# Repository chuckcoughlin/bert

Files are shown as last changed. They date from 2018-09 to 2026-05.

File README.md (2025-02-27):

## bert
"Bert" is a DIY robot development project based on the open-source version of the [Poppy](https://www.poppy-project.org/en/) platform developed by [Generation Robots](https://www.generationrobots.com/en/278-poppy-humanoid-robot). Bert is a reduced stature (83cm) humanoid. The name is assigned in the hope that the robot will dance as Dick van Dyke's character in "Mary Poppins". We have a long ways to go.

 For further details see the [architecture](http://github.com/chuckcoughlin/bert/tree/master/docs/architecture.md), [toolchain](https://github.com/chuckcoughlin/bert/tree/master/docs/toolchain.md), [test plan](https://github.com/chuckcoughlin/bert/tree/master/docs/testplan.md) and [user-guide](http://github.com/chuckcoughlin/bert/tree/master/docs/user-guide.md) documents.
 The test plan contains current testing status and is a good indication of the project's progress. A prior version of the robot written in `Java` for the `Odroid-XU4` processor is stored on the `version1` branch. The current version is written in `Kotlin` for the `Odroid-N2+`

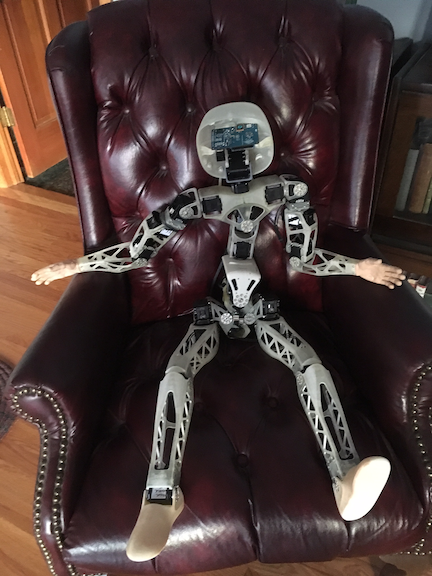
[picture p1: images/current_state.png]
Bert
 
 ```                  Bert - Most Recent Picture     ```

Video clips showing representative capabilities are available at the following links:
 * [Sample voice interaction](https://www.youtube.com/watch?v=ZoP7b5YDawg)
 * [Creating a pose](https://www.youtube.com/watch?v=3lilrxy11Ac)

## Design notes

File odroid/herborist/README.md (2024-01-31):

# Herborist
Herborist is a graphical tool that helps you detect and configure Dynamixel motors for Poppy creatures or other robotic projects. 

More precisely, Herborist can be used to:

* Find and identify available serial ports
* Scan multiple baud rates to find all connected motors
* Modify the EEPROM configuration (of single or multiple motors)
* Make motors move (e.g. to test the angle limits).

**Compatible motors:** Identical to `pypot`: MX-106, MX-64, MX-28, MX-12, AX-12, AX-18, RX-24, RX-28, RX-64, XL-320, SR-RH4D, EX-106. Derivated versions are also supported (e.g. MX-28AT, MX-28R, MX-28T, ...).

Install herborist with `pip install herborist` and run it with command `herborist`:

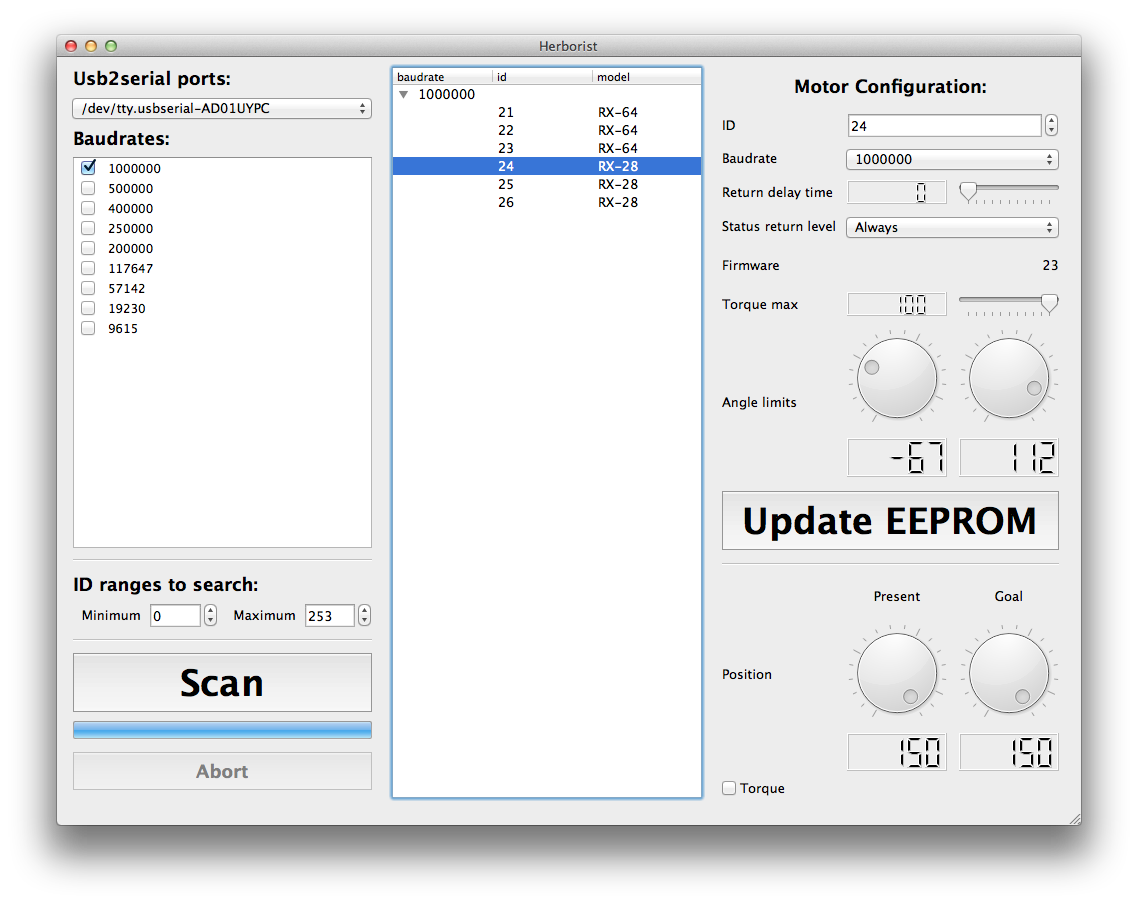
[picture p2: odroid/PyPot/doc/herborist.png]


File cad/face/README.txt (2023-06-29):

Steps to create the face model.

1) Starting with the Poppy skeleton/head/head_face.stl
2) Import 1) into Blender. Scale to mm. Set origin, rotation. Remove all non-manifold
   vertices. Save as face_raw.blend. Export as face_raw.stl.
3) Run OpenScad, blocked_face.scad. This reads head_face.stl and blocks off portions of
   the face to be saved. Export the block shapes only as blocks.stl.
4) Import 2) and 3) into Blender. Use boolean operators to save the intersection of 
   the blocks and the raw face. Clean up any block remnants. Save as collar.blend 
   and export as collar.stl.
5) Fill the top open space by selecting points around the perimeter and "new face 
   from vertices". For each of the three faces, loop-cut and separate. Save as 
   collar-face.blend.
6) From 5) Delete the collar (We will merge at the end). Merge the 3 faces into
   a single object. Lock down perimeter. Save as face-only.blend. 
7) Select the outer edge of the three planes. From the "Mesh" menu add a convex hull. 
   Delete the part of the hull that is on the backside. From the "vertex" menu
   select "bevel", in turn, for each of the two nodes that radiate a large number
   of edges. Save as "face-mesh'.

Alternate
Files named cartoon_head have been purchased from TurboSquid under their 3D Model License (https://blog.turbosquid.com/turbosquid-3d-model-license). Product ID: 1912829. "You can use the model for both non-commercial and commercial purposes. You can use it for multiple projects, forever(more informations under license)."

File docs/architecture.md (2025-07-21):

# High-level Design and Software Architecture

Control software embedded in the "Bert" project takes its inspiration from the [Poppy Humanoid](https://www.poppy-project.org) project at
[Generation Robots](https://www.generationrobots.com/en/278-poppy-humanoid-robot). Our implementation deviates significantly, however. The core language is Kotlin instead of C++ and Python. The feature-set has been greatly simplified - and we have added natural-language speech processing with the integration of an Android tablet.

The *Poppy*  project is described in detail in the thesis ["Poppy: open-source, 3D printed and fully-modular
robotic platform for science, art and education"](https://hal.inria.fr/tel-01104641v1/document) by Matthieu Lapeyre. A full list of project authors may be found at: <https://github.com/poppy-project/poppy-humanoid/doc/authors.md>.

The bulk of this document addresses various design issues and approaches to their solutions (or lack thereof)

***
## Table of Contents <a id="table-of-contents"/>
  * [Target Hardware](#hardware)
    * [Odroid](#odroid)
    * [Android](#android)
    * [Raspberry Pi](#raspberry)
  * [Software Architecture](#architecture)
    * [ANTLR](#antlr)
    * [Configuration](#configuration)
    * [URFD](#geometry)
    * [Dynamixel Servos](#dynamixel)
    * [Open AI](#ai)
  * [Design Considerations](#design)
    * [Control](#control)
    * [Messaging](#messages)
    * [Forward Kinematics](#forward)
    * [Inverse Kinematics](#inverse)
    * [Poses](#poses)
  * [Appendices](#appendices)
    * [Rationale for Kotlin](#whykotlin)
    * [Failures](#failures)

***
## Target Hardware 
[toc](#table-of-contents)

#### Odroid  
The robot's central processor is a single-board Linux computer, an Odroid N2+.

#### Android 

A Samsung Galaxy Tablet S8+, model SM-X800 is used as the speech processor. It converts spoken input into command strings used to control the robot. It also converts textual responses from tne robot into audible speech. The tablet is Android version 13, SDK version 33.

#### Raspberry Pi 

A Raspberry Pi version 5 serves as a "fine motor controller". For smaller parts, currently eyes and
eyelids.

## Software Architecture 
[toc](#table-of-contents)

Here is a diagram that shows the major software components.

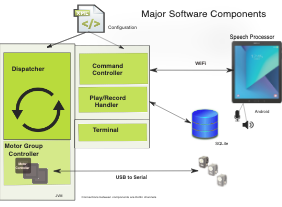
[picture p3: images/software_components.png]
Major Software Components

```                        Development - System Architecture ```

#### ANTLR  
*ANTLR* is a parsing framework explained [here](https://www.antlr.org). It is used to convert
streams of tokens from spoken text into commands for the robot.

#### Configuration 
Robot attributes and connectivity are defined in an .xml file, *bert.xml*. A representative
example is shown below.
The file is read by each of the independent processes, giving them a common understanding
of site-specific parameters and attributes of the robot.

Substitution parameters, @...@, are replaced with site-specific values during the build.
```
<?xml version="1.0" encoding="UTF-8"?>

<!-- This file describes "bert", a poppy-like robot. The identical configuration
     is used for both the server and client-side processes.
 -->
 <?xml version="1.0" encoding="UTF-8"?>

 <!-- This file describes "bert", a robot derived from the Poppy project.
 	 This identical configuration is used for each of the independent processes.
  -->
 <robot>
 	<!-- This first section lists miscellaneous properties. @...@ values are
 	     replaced by the build scripts.
 	-->
 	<property name="name">bert</property>
 	<property name="release">@RELEASE@</property>
 	<property name="date">@DATE@</property>
 	<!--  Socket port used by the bluetooth RFCOMM server  -->
 	<property name="blueserver">11046</property>
 	<!--  Cadence in msecs refers to the record frequency  -->
 	<property name="cadence">1000</property>
 	<!--  Name of machine hosting the server process  -->
 	<property name="hostname">localhost</property>
 	<!--  Used by the terminal  -->
 	<property name="prompt">bert: </property>

  <!-- For the "Command" controller, defines the bert  TCP socket. The device UUID
	     must match the hardcoded value in tablet code, the well-known bluetooth UUID
	     for RFCOMM. -->
	<controller name="command" type="COMMAND"
		socket="bert" hostname="localhost"  port="11046" uuid="1101-0000-2000-8080-00815FAB34FF">
	</controller>
	<controller name="terminal" type="TERMINAL" prompt="bert:"/>

 	<!-- These controllers manage groups of joints. Requests are sent the entire group at once across
 	     a serial connection. The names must exist in the enumeration bert.share.motor.Joint.
 	     There is an upper body group and a lower body group.
     -->
 	<controller name="lower" type="SERIAL">
 		<port  name="lower" device="@PORT_LOWER@" />
 		<joint name="LEFT_ANKLE_Y" type="MX28" id="15" offset="-91" min="60" max="135" orientation="direct" />
 		<joint name="LEFT_HIP_X"   type="MX28" id="11" offset="-8" min="155" max="205" orientation="indirect" />
 		<joint name="LEFT_HIP_Y"   type="MX64" id="13" offset="-18" min="75" max="225" orientation="direct" />
 		<joint name="LEFT_HIP_Z"   type="MX28" id="12" offset="-200" min="-20" max="45" orientation="indirect" />
 		<joint name="LEFT_KNEE_Y"      type="MX28" id="14" offset="-4" min="50" max="180" orientation="indirect" />
 		<joint name="RIGHT_ANKLE_Y"    type="MX28" id="25" offset="-108" min="60" max="135" orientation="indirect" />
 		<joint name="RIGHT_HIP_X"      type="MX28" id="21" offset="16" min="155" max="205" orientation="direct" />
 		<joint name="RIGHT_HIP_Y"      type="MX64" id="23" offset="-18" min="75" max="225" orientation="indirect" />
 		<joint name="RIGHT_HIP_Z"      type="MX28" id="22" offset="-160" min="-20" max="45" orientation="direct" />
 		<joint name="RIGHT_KNEE_Y"     type="MX28" id="24" offset="15" min="50" max="180" orientation="direct" />
 	</controller>
 	<controller name="upper" type="SERIAL">
 		<port  name="upper" device="@PORT_UPPER@" />
 		<joint name="LEFT_ARM_Z"   type="MX28" id="43" offset="0" min="-105" max="45" orientation="indirect" />
 		<joint name="LEFT_ELBOW_Y" type="MX28" id="44" offset="17" min="45" max="180" orientation="direct" />
 		<joint name="LEFT_SHOULDER_X"  type="MX28" id="42" offset="-70" min="90" max="180" orientation="direct" />
 		<joint name="LEFT_SHOULDER_Y"  type="MX28" id="41" offset="-65" min="-120" max="155" orientation="direct" />
 		<joint name="RIGHT_ARM_Z"      type="MX28" id="53" offset="0" min="-105" max="45" orientation="direct" />
 		<joint name="RIGHT_ELBOW_Y"    type="MX28" id="54" offset="4" min="45" max="180" orientation="indirect" />
 		<joint name="RIGHT_SHOULDER_X" type="MX28" id="52" offset="-105" min="90" max="180" orientation="indirect" />
 		<joint name="RIGHT_SHOULDER_Y" type="MX28" id="51" offset="-100" min="-155" max="120" orientation="indirect" />
 		<joint name="HEAD_Y"       type="AX12" id="37" offset="-120" min="-5" max="20" orientation="direct" />
 		<joint name="HEAD_Z"       type="AX12" id="36" offset="-150" min="-30" max="30" orientation="indirect" />
 		<joint name="ABS_X"        type="MX64" id="32" offset="0" min="150" max="210" orientation="direct" />
 		<joint name="ABS_Y"        type="MX64" id="31" offset="16" min="150" max="210" orientation="direct" />
 		<joint name="ABS_Z"        type="MX28" id="33" offset="-160" min="-60" max="60" orientation="direct" />
 		<joint name="BUST_X"       type="MX28" id="35" offset="5" min="150" max="210" orientation="direct" />
 		<joint name="BUST_Y"       type="MX28" id="34" offset="24" min="150" max="210" orientation="direct" />
 	</controller>
 </robot>
```

#### URDF 
The geometry of the robot is used for trajectory planning, balance and other purposes. It is inspired by the
Unified Robot Description Format](http://wiki.ros.org/urdf/XML) (URDF) file.  A sample, specific to _Poppy_, may be found [here](https://github.com/poppy-project/poppy-humanoid/blob/master/hardware/URDF/robots/Poppy_Humanoid.URDF). We have modified the format freely for our own purposes.

We have added the IMU location and taken other liberties with the standard (e.g. angles in degrees to match
the Dynamixel output). Joint orientations are defined via a unit vector showing the alignment. The axes
form a right-handed rool, pitch, yaw coordinate system as follows:

| Axis | <center>Description</center> |<center>Positive</center>
| :--: | :---------------------- | :-------------: |
| x | Front-to-back | Front |
| y | Side-to-side | Robot's Right |
| z | Vertical | Up |

Note that in order to be symmetric with respect to the vertical centerline, some
joints are defined in an inverse direction. Links are
names of the "bones" between joints. As series of joints
and links form a "limb".
```
<?xml version="1.0" encoding="utf-8"?>
<!--
	Right-handed coordinate system: x positive to front, y positive to right, z positive up
	- axis is unit vector around which joint rotates clockwise
   	- lengths ~ mm, angles ~ degrees -->
<robot name="bert">
	<!-- The Internal Measurement Unit (IMU) is the world-frame origin. Its position is always (0,0,0).
	     This origin is located in the pelvis midway between the hip sockets and back to align with the
	     left/right hip y axis. The orientation of the IMU is with respect to the robot reference frame.
	     It may be altered by setting IMU quaternion roll,pitch,yaw directly and then updating.
	-->
	<imu rpy="0. 0. 0."/>
	<!-- A link is roughly equivalent to a bone. A link connects a source pin (joint)
	     to a joint or end effector. The parent link is a joint (a REVOLUTE link pin).

	    Links form a tree from the IMU terminating in the various end effectors.
		Joint names must match the names in bert.xml.

		Link (end-pin) coordinates are relative to the source pin ~ mm. The y-axis coincides with the joint axis
		with the origin at the mid-point, positive to the left. The link z axis is always perpendicular to the joint
		axis corresponding to the y-axis "home" position, positive up. "home" is where the robot stands straight up.
		The x-axis juts forward perpendicular to the z-axis (positive forward).

		The "rpy" settings (roll, pitch, yaw) define the orientation of the motor or end-effector with respect to
		the source pin. The order of rotations is: roll, pitch, yaw. The "rpy" settings do not affect the location
		of the end-pin, only its orientation. Use right-hand rule to determine direction.
		     roll  - rotation about the x axis
		     pitch - rotation about the y-axis
		     yaw   - rotation about the z-axis

		Joints are named for the robot axis about which they rotate when viewed in the "home" position.

	  -->
	<link side="FRONT">        <!-- root -->
		<joint name="RIGHT_HIP_X"
			   xyz="0.0 22.5417390633467 0.0"  rpy="0. 0. 90." home="180.0"/>
		<joint name="LEFT_HIP_X"
			   xyz="0.0 -22.5417390633466 0.0" rpy="0. 0. 90." home="180.0"/>
		<joint name="ABS_Y"
			   xyz="12.0 0.0 62.0"             rpy="0. 0. 0." home="180.0"/>
		<source joint="IMU" />
	</link>
	<link side="RIGHT">
		<joint name="RIGHT_HIP_Z"          home="0.0"
			   xyz="43.9986 5.0 0.0" rpy="0. 0. 90."/>
		<source joint="RIGHT_HIP_X" />
	</link>
	<link side="RIGHT">
		<joint name="RIGHT_HIP_Y"
			   xyz="0.0 0.0 24.0" rpy="0. 0. 0." home="180.0"/>
		<source joint="RIGHT_HIP_Z" />
	</link>
	<link side="RIGHT">
		<joint name="RIGHT_KNEE_Y"
			   xyz="0.0 0.0 182.0"  rpy="0. 0. 0." home="180.0"/>
		<source joint="RIGHT_HIP_Y" />
	</link>
	<link side="RIGHT">
		<joint name="RIGHT_ANKLE_Y"
			   xyz="0.0 0.0 -180.0"  rpy="0. 180. 0." home="90.0"/>
		<source joint="RIGHT_KNEE_Y"/>
	</link>
	<link side="RIGHT">
		<appendage name="RIGHT_TOE"
				   xyz="95. -15.0 -35.5" rpy="180. 90. 180."/>
		<appendage name="RIGHT_HEEL"
				   xyz="-43.0 12.0 -35.5" rpy="180. 90. 180."/>
		<source joint="RIGHT_ANKLE_Y"/>
	</link>
	<link side="LEFT">
		<joint name="LEFT_HIP_Z"
			   xyz="-43.9986 5.00 0.0" rpy="0. 0. 90." home="180.0"/>
		<source joint="LEFT_HIP_X"/>
	</link>
	<link side="LEFT">
		<joint name="LEFT_HIP_Y"
			   xyz="0.0 0.0 24.0"       rpy="0. 0. 0." home="180.0"/>
		<source joint="LEFT_HIP_Z"/>
	</link>
	<link side="LEFT">
		<joint name="LEFT_KNEE_Y"
			   xyz="0.0 0.0 182.0" rpy="0. 0. 0." home="180.0"/>
		<source joint="LEFT_HIP_Y"  />
	</link>
	<link side="LEFT">
		<joint name="LEFT_ANKLE_Y"
			   xyz="0.0 0.0 -180.0" rpy="0. 180. 0." home="90.0"/>
		<source joint="LEFT_KNEE_Y" />
	</link>
	<link side="LEFT">
		<appendage name="LEFT_TOE"
				   xyz="95. 15.0 -35.5"  rpy="180. 90. 180."/>
		<appendage name="LEFT_HEEL"
				   xyz="-43. -12.0 -35.5" rpy="180. 90. 180."/>
		<source joint="LEFT_ANKLE_Y" />
	</link>
	<link side="FRONT">
		<joint name="ABS_X"
			   xyz="0.0 0.0 8.0" rpy="0.0 180.0 90.0" home="180.0"/>
		<source joint="ABS_Y"/>
	</link>
	<link side="FRONT">
		<joint name="ABS_Z"
			   xyz="0.0 12.0 51.6374742" rpy="90. 90.0 0.0" home="0.0"/>
		<source joint="ABS_X" />
	</link>
	<link side="FRONT">
		<joint name="CHEST_Y"
			   xyz="-2.8 79.85 0.0"  rpy="-90. 90. 90." home="180.0"/>
		<source joint="ABS_Z" />
	</link>
	<link side="FRONT">
		<joint name="CHEST_X"
			   xyz="0.0 8.0 0.0" rpy="90. 180. -90." home="180.0"/>
		<source joint="CHEST_Y"/>
	</link>
	<link side="FRONT">
		<joint name="NECK_Z"
			   xyz="-5.0 0.0 84.0"    rpy="90. -90. 0." home="180.0"/>
		<joint name="LEFT_SHOULDER_Y"
			   xyz="-4.0 -77.1 50.0"  rpy="0. 0. 90." home="0.0"/>
		<joint name="RIGHT_SHOULDER_Y"
			   xyz="-4.0 77.1 50.0"  rpy="0. 0. 90." home="0.0"/>
		<source joint="CHEST_X" />
	</link>
	<link side="FRONT">
		<joint name="NECK_Y"        home="0.0"
			   xyz="-0.0 20.0 20.0"  rpy="-90. 0. -90."/>
		<source joint="NECK_Z"/>
	</link>
	<link side="FRONT">
		<appendage name="LEFT_EYE"
				   xyz="0.0 32.0 55.0" rpy="0. 0. 0."/>
		<appendage name="RIGHT_EYE"
				   xyz="0.0 -32.0 55.0"  rpy="0. 0. 0."/>
		<appendage name="LEFT_EAR"
				   xyz="-30.0 62.0 55.0" rpy="0. 0. 0."/>
		<appendage name="RIGHT_EAR"
				   xyz="-30.0 -62.0 55.0"/>
		<appendage name="NOSE"
				   xyz="15.0 0.0 40.0" rpy="0. 0. 0."/>
		<source joint="NECK_Y"  />
	</link>
	<link side="LEFT">
		<joint name="LEFT_SHOULDER_X"
			   xyz="-28.4 0.0 0.0" rpy="0. 90. 90." home="180.0"/>
		<source joint="LEFT_SHOULDER_Y" />
	</link>
	<link side="LEFT">
		<joint name="LEFT_SHOULDER_Z"
			   xyz="0.0 18.5 -83.0"  rpy="0. 90. 90." home="180.0"/>
		<source joint="LEFT_SHOULDER_X" />
	</link>
	<link side="LEFT">
		<joint name="LEFT_ELBOW_Y"
			   xyz="81.175 0.0 10.0"  rpy="0. 90. 180." home="180.0"/>
		<source joint="LEFT_SHOULDER_Z" />
	</link>
	<link side="LEFT">
		<appendage name="LEFT_FINGER"
				   xyz="4.99 -6.915 -121.0" rpy="0. 90. 0.0"/>
		<source joint="LEFT_ELBOW_Y" />
	</link>
	<link side="RIGHT">
		<joint name="RIGHT_SHOULDER_X"
			   xyz="28.4 0.0 0.0" rpy="0. 90. 90." home="0.0"/>
		<source joint="RIGHT_SHOULDER_Y"/>
	</link>
	<link side="RIGHT" >
		<joint name="RIGHT_SHOULDER_Z"
			   xyz="0.0 18.5 83.0" rpy="0. 90. 90." home="180.0"/>
		<source joint="RIGHT_SHOULDER_X"/>
	</link>
	<link side="RIGHT">
		<joint name="RIGHT_ELBOW_Y"
			   xyz="81.175 0.0 10.0" rpy="0. 90. 180." home="180.0"/>
		<source joint="RIGHT_SHOULDER_Z"/>
	</link>
	<link side="RIGHT" >
		<appendage name="RIGHT_FINGER"
				   xyz="4.99 6.915 -121.0" rpy="-90. 90. -90.0"/>
		<source joint="RIGHT_ELBOW_Y" />
	</link>
</robot>
```
Some dimensions were taken from the [Poppy URDF](https://github.com/poppy-project/poppy-humanoid/blob/master/hardware/URDF/robots/Poppy_Humanoid.URDF), others were measured directly.

Analysis of this file, results in a description of the robot as a tree or
"chain" of links. The tree has a single origin in the center of the pelvis. There are
multiple terminations or "end effector" (e.g. finger or toe). The links represent limbs of the body (e.g "thigh").
A quaternion transform matrix is calculated for each link, describing its orientation and size with respect to
the parent joint.

Calculation of end-effector location is accomplished via Quaternion multiplication up the chain.

#### Dynamixel Servos  
The control motors are Dynamixel MX-64, MX-28 and AT-12A models from [Robotis](http://en.robotis.com).
The servos feature their own PID control. A single write of a target position, speed and torque is all that is
required for control. There is no need for a constant refresh action.
A further efficiency is provided by the *SYNC WRITE* directive. This allows control of multiple motors
with a single command, as long as the affected motors are daisy-chained on the same serial port. A
*SYNC WRITE* command does not return status.

We use version 1.0 of the protocol as the motors were delivered with that version.

Idiosyncrasies:<br/>
  * There appears to be a maximum write frequency, especially for the AT-12A motors. We guarantee at least 50ms between consecutive writes to the same serial port. The symptom is dropped responses.
  * There is no guarantee that responses from the serial port correlate 1:1 with the requests. The
   response buffer can hold partial replies or several replies combined.

#### Open AI  
 The interface with [Chat GPT](https://openai.com/chatgpt/overview)  is incidental to the operation
 of the robot. It is used simply to add completion to queries or commands that would be otherwise not understood
 by the robot. In order to use the AI interface you must create an account and obtain a key from from `Open AI`
 and place it in the environment on the robot (e.g. in ~/.bashrc) as CHATGPT_KEY.

## Design Considerations <a id="design"/>

#### Control <a id="control"/>
[toc](#table-of-contents)

The main robot process is a Kotlin application running on the Odroid processor.
Major components, _terminal_,_command_, and _dispatcher_ are Kotlin co-routines
communicating over Channels. The messages passed back and forth between these processes are instances of class _MessageBottle_.
Communication with the tablet process is via text messages across a Wi-Fi
socket.

There are numerous situations in the robot where a single user command results in multiple motor commands internally. For example, whan the robot has been relaxed,
all positional information is lost. So when re-enabling torque, the joint angle information must be re-read to keep it up-to-date.
Another example is *pose* commands that are split into separate
directives for each limb.

Moreover, it is important tnat the ``MotorController`` not be given a command until the serial callback of the previous has been received.
A new request must not
submitted until the ``MotorConrtoller`` finishes with the previous request.
The sequencing function as well as command expansion is handled by an ``InternalController`` which queues requests and inserts required supporting requests as necessary.

#### Messaging
The tablet executes a Wi-fi client based on Java classes that are a standard part of the Android SDK. It connects to the robot process via sockets.

Messages that are intended to be spoken or logged are prepended
with a 4-character header followed by ASCII text.
Messages have a 1K-byte
size limit and are stripped of any trailing whitespace except for a terminating new-line.

More complicated messages intended for inter-process communication have
a similar header followed by a string indicating type and then JSON
text.

Header values are described in the table below:

| Header	| <center>Description</center>|
| -------- | :------------------------------------------------------------------ |
|MSG:|	Message from the tablet to the robot. Plain english request or query.	|
|ANS:|	Reply from the robot. This text is meant to be spoken and appear on the transcription log. |
|JSN:|	Communicate via JSON objects. These messages direct robot-tablet communication, not meant for enunciation.	|
|LOG:|	System message from the robot meant to appear on the tablet's log panel. |
|TBL:|	Define a table to show on the tablet's table panel. Pipe-delimited fields contain: title, column headings. |

Several messages may be buffered in the same socket transmission to or from the tablet. However, the
sender appends a new-line to each message to enable both the tablet and robot
Kotlin code to use a custom `readline()` routine to parse one message at a time.

#### Forward Kinematics 
Forward kinematics refers to the calculation of the 3D position of joints and end effectors based
on the connections of skeletal components and joint angles. The calculations are derived from
<ins>Introduction to Robotics</ins>  by S. K. Saha and
facilitated by the blog post [How to Calculate a Robot's Forward Kinematics in 5 Easy Steps](https://blog.robotiq.com/how-to-calculate-a-robots-forward-kinematics-in-5-easy-steps) by Alex Owen-Hill.

Refering to the URDF.xml file (listed above) *link* elements:

| Parameter	| <center>Description</center> |
| -------- | :------------------------------------------------------------------ |
|d| distance from the link's source pin to the REVOLUTE center in the z direction. |
|r| length of the common normal between source and link center z axes|
|alpha| the angle along the common normal between previous and current z axis |
|theta| the angle of the limb x axis with respect to the source pin|
|xyz| coordinates from source to REVOLUTE center |

Lengths are ~mm, angles in degrees. The z direction is always the axis of rotation of the motor.

#### Inverse Kinematics 
Optimal trajectory planning, such as the Poppy example [here]
(https://github.com/Phylliade/ikpy/tree/master/src/ikpy) by Pierre Manceron is known to be complex and slow. We go to great lengths to avoid it.

#### Poses 
A "pose" is a position of the robot as a whole, comprising settings for each of its joints. Poses may be
generated offline or as a result of recording joint values when the robot has been manually positioned for some
purpose.  For each joint, the pose records torque, speed and position. Torque and speed are in percent
of maximum and position is in degrees. Torque is a measure of how pliant the joint is. Speed refers to
how fast the motor will move to the desired position. All values are integers. Null values
imply that the current setting will not be changed. Not all parameters are required.

| Name	| Parameter	| ABS_X	| ABS_Y |	ABS_Z ...
| -------- | --------- | ------- | ------ | ------
|relaxing|	torque	|0	|0
|standing|	position|	0	|90
|standing|	speed	|25|	null
|standing|	torque	|100|	75

``Partial View of a Sample "Pose" Table``

In the sample database table shown above, only 3 of the 25 actual joints are shown. The "relaxed" pose contains
only the single line to set torque to a zero setting. This effectively renders the robot limp.
The "standing" setting defines all three parameters. Note that the ABS_Y speed is null. This
means that for ABS-Y the speed at which it travels to 90 degrees is the same as the last
time the joint was used. On power-up speeds are 100% and torques are 0%. Unless specified in
the pose, torques are automatically set to 100% whenever a joint is moved.

When moving to a set pose, it is usually sufficient to simply use that pose as a goal and move
to it directly using a single command to the servos. For the most part, collision conflicts are
avoided by limits on the angular motion of the joints.  For situations not covered in this way, we have adopted a simple set of heuristic tests that are applied prior to each movement. In general,
these heuristics insert intermediate poses to avoid conflicts en route or truncate motion when the goal
is itself a conflict. We avoid a full trajectory optimization.

*** Raspberry Pi ***</br>
An additional processor, a Raspberry Pi, is placed in the
cranium on top of the main Odroid processor. The RPi
is a "fine motor controller" used for control of smaller
appendages, e.g. eyes.

## Appendices 
[toc](#table-of-contents)
#### Why Kotlin?
In the "Poppy" [thesis](https://hal.inria.fr/tel-01104641v1/document) (section 7.4.1 and following), the author considers use of the Robot Operating System (ROS) for the core software and concludes that it is overly complex and inefficient. This coincides with my own experience with [sarah-bella](https://github.com/chuckcoughlin/sarah-bella). Moreover, I discovered that, at least with Android, ROS messaging was not reliable. Messages were dropped under high load, a situation not acceptable for control applications.

This same author noted that the "Pypot" software developed in Python for Poppy had severe performance limitations that placed strict limits on its design.

While I can't simply try all the designs, [YARP](http://www.yarp.it/index.html) used by the "iCub" project seemed closest to my perceived needs. It is written in C++ and is loaded with features that I'll never use. Given my failure to create a cross-compilation environment, I've decided to let a simplified *YARP* serve as an inspiration for a Kotlin-based solution. For simplicity, the ancillary code will be Kotlin also.

The previous version was written entirely in Java. However I decided to
write the current iteration of the project in Kotlin for the following reasons:
  * The Android platform identifies Kotlin as a core language
  * The threading model seems much more straightforward
  * It is possible to automatically convert Java to Kotlin
  * It was time for me to learn something new

Why did I select Java for the original project when the iCub project chose Python?
  * Familiarity - over 2 decades of working with Java
  * Refactoring - the refactoring capabilities of IntelliJ are unparalleled, in my opinion, and make code re-structuring quick, easy and accurate
  * Code-Debug-Cycle - problems are more likely to be discovered by the compiler rather than run-time as with Python
  * Debugging - via IntelliJ we can set breakpoints and inspect run-state not only locally, but on the target robot
  * Performance - Java executes an order of magnitude faster than Python
  * Threading - the Java threading model is more straightforward (IMHO)
  * Cross-compiling - difficulties creating Odroid executables precluded my use of C++.

### Failures 
[toc](#table-of-contents)

This section documents ideas that were tried and abandoned. The implication here is not
so much that these ideas won't work, but rather that I couldn't get them to work or found
more expedient alternatives.

*** Gradle *** <br/>
``Gradle`` is a modern tool for building software of several flavors.  To install ``Gradle`` use ``homebrew``:
```
     brew install gradle
     brew install gradle-completion
```
I totally failed to create a C++ build script for cross-compilation (Mac to Odroid). Moreover after nearly a week of trying, I gave up on the Java building also. I was unable to create an environment to conveniently share re-usable code among separate top level targets. I'm sure it can be done, I just lost interest. *ant* does everything I need.

*** Cross-compilation *** <br/>
On the build machine, I downloaded [GNU Embedded Toolchain for ARM]( https://developer.arm.com/open-source/gnu-toolchain/gnu-rm/downloads), then followed the installation steps outlined [here](https://gnu-mcu-eclipse.github.io/toolchain/arm/install/#macos-1), Using a *makefile* and these tools, I compiled C++ code for the Odroid X64. It had a bad format and didn't execute. I gave up on C++ in favor of Java for the core control loop.

*** Cmake *** <br/>
The [TinyB](https://github.com/intel-iot-devkit/tinyb ) library for Bluetooth integration came with build files for *cmake*.
I was unable to get a successful compilation of the JNI code on the Odroid. I followed the directions [here](http://fam-haugk.de/starting-with-bluetooth-le-on-the-raspberry-pi) and [here](http://www.martinnaughton.com/2017/07/install-intel-tinyb-java-bluetooth.html) with
modifications for the Odroid and Java11. With these installs which literally took
hours and used up over 10% of available disk space,  the _cmake_ build still never completed successfully.
```
sudo apt-get install libgtk2.0-dev
sudo apt-get install pkg-config
sudo apt-get --purge autoremove cmake
sudo apt-get install build-essential
cd ~
wget http://www.cmake.org/files/v3.14/cmake-3.14.0.tar.gz
tar -xzf cmake-3.14.0.tar.gz
cd cmake-3.14.0
./configure
make
sudo make install
hash -r

export JAVA_AWT_LIBRARY=$JAVA_HOME/lib/libawt.so
export JAVA_JVM_LIBRARY=$JAVA_HOME/lib/server/libjvm.so
export JAVA_INCLUDE_PATH=$JAVA_HOME/include
export JAVA_INCLUDE_PATH2=$JAVA_HOME/include/linux
export JAVA_AWT_INCLUDE_PATH=$JAVA_HOME/include
```
Since the purpose of all this was to generate a Makefile of about 50 lines, I
did it the old-fashioned way and edited it by hand, to use `make` directly.

*** Herborist *** </br>

Herborist is a tool for configuring Dynamixel servos. The [toolchain](https://github.com/chuckcoughlin/bert/tree/master/docs/toolchain.md) document describes an Ubuntu installation using *pip*, but, for me, the install of the PyQt5 package failed and, subsequently, the *herborist* install. As a workaround, I copied the code (pure python) and ran it directly.
```
   cd
   cd src/herborist
   python3 setup.py build
   sudo chmod 777 /usr/local/lib/python3.10/dist-packages
   sudo chmod 666 /usr/local/lib/python3.10/dist-packages/easy-install.pth
   sudo chmod 777 build.bdist.linux-aarch64
   sudo chmod 777 /usr/local/bin
   python3 setup.py install
```
This failed to run, also. My workaround is to use a command-line tool in the *PyPot* distribution for servo
configuration.

*** JBlueZ ***<br/>
JBlueZ](http://jbluez.sourceforge.net/)
by Edward Kay is a minimalist
implementation of a Bluetooth interface. Its intent is to use JNI and link directly
to _libbluetooth.so_. However, it requires J2ME which is not the Java on the Odroid.
It also relies on _DBus_ which is yet-another-interface to learn and debug. It
also comes with a GPL license.

The version1 code had this working, but broke with the current Bluetooth version (BlueZ 5.48). Instead of
debugging yet again, we elected to drop Bluetooth communication in favor simple socket-socket communication
over WiFi. The realization that a WiFi network could be established anywhere with a cell phone "local hotspot"
removed the need for bluetooth between robot and tablet.

Programmatic access to Bluetooth requires a interface to the Odroid's
bluetooth library `libbluetooth.so` .
An excellent introduction is a book by Albert Huang
of MIT published [here](http://people.csail.mit.edu/albert/bluez-intro/).
 Starting with Albert's examples and relying
heavily on lessons learned trying to implement the various packages
mentioned in my "Failures" section (See [Software Architecture](http://github.com/chuckcoughlin/bert/tree/master/docs/architecture.md)), I developed a custom, minimalist
daemon using RFCOMM. It communicates with the Kotlin application over sockets and
the tablet via Bluetooth.
Its sole purpose is to transfer strings between the tablet and the Odroid robot application.
The tablet uses standard Android Bluetooth classes.

On the development machine, in the _IntelliJ_ Configuration project, the ``install_odroid_source`` script
copies C source files onto the Odroid in preparation for building _blueserverd_, the
daemon, and _blueserver_, an interactive test application. (This script may have to be modified for
the correct robot home directory on the Odroid).

Then to build on the Odroid, from the directory containing the source projects -
```
  cd blueserver
  make -e
  make install
  cd ${BERT_HOME}/bin
  sudo ./install_blueserver_init_scripts
```

Configure Bluetooth using the robot's pull-down menu. Configure the adapter so that it is always visible (discoverable) and give it a "friendly"
name of "bert". Pairing is based on the friendly name and can be initiated
either from the robot or the tablet. The ```bluetoothctl``` tool is available for command-line configuration.

Add the following lines to _/etc/dbus-1/system.d/bluetooth.conf_ under ``<policy context="default">``:

```
  <allow send_interface="org.bluez.GattService1"/>
  <allow send_interface="org.bluez.GattCharacteristic1"/>
  <allow send_interface="org.bluez.GattDescriptor1"/>
```

Note that _blueserver.h_ has the bluetooth address of the tablet hard-coded. On the tablet
the device should be configured as ``bert``. On the Odroid the adapter is also known as ``bert``.

The init script launches the _blueserverd_ daemon. Connection difficulties may arise if too many bluetooth-enabled
devices are in range leading to incorrect pairings. If so, the Odroid system may report
"DbusFailedError: host is down".

*** TinyB *** </br>
[TinyB](https://github.com/intel-iot-devkit/tinyb ) is a library and Java classes for Bluetooth LE communication.
 The original distribution builds with `cmake`, but I was never
able to get that working. I just created a custom `Makefile` to build the code.
and integrate it with the main robot application.

Unfortunately when loading the JNI library ...
```
      UnsatisfiedLinkError:  g_cclosure_marshall_generic
        in tinyb.BluetoothManager.getNativeAPIVersion
          BluetoothManager.getBluetoothManager
```
The underlying issue is that the missing method was introduced in libc6 2.30.
The Odroid has 2.27. I get this error on all native methods. I assume it is a
result of using C++ in the interface library.

*** Bluecove ***</br>
*BlueCove* is yet another Bluetooth library available from [here](https://code.google.com/archive/p/bluecove/wikis/Documentation.wiki). A well written example for a simple connection is written by [Luu Gia Thuy](
https://github.com/luugiathuy/Remote-Bluetooth-Android/blob/master/RemoteBluetoothServer/src/com/luugiathuy/apps/remotebluetooth)

Unfortunately the project jar files contained too many dependencies to modularize into Java 10 jars.
I decided to build the jar from scratch, adding classes as necessary. I converted logging to java.util.logger (removing _log4j_ dependencies). I removed the Java dependency on J2ME.

The standard jar files included the "stacks", native library code for different target architectures,
though not the one we needed, for ARM. Consequently I had to build from source using code
that brought on a GPL dependency.

This just got too complicated.

*** GATT *** <br/>
Since we don't need a full-featured Bluetooth interface, the idea was to simplify things
considerably by making use of GATT (Generic Atributes)
Bluetooth profiles. The only characteristics we require are two to read and write
simple strings. Following instructions [here](https://stackoverflow.com/questions/25427768/bluez-how-to-set-up-a-gatt-server-from-the-command-line), we attempted to create a GATT server on the Odroid using
 _bluetoothctl_. The reported syntax for setting service characteristics in _bluetoothctl_
 didn't work and I was never successful in creating a registration.

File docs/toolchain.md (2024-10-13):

# Skeleton and Toolchain

This document describes the software tools used to develop "Bert", including their procurement and configuration. It also gives a step-by-step guide to assembly of the skeleton, including visual aids.

"Bert" is a based on the [Poppy](https://www.poppy-project.org) platform from
[Generation Robots](https://www.generationrobots.com/en/278-poppy-humanoid-robot).  *Poppy* is supplied in open-source format, both hardware and software. Version 1.0.2 source is at: <https://github.com/poppy-project/poppy-humanoid>. The repository contains both hardware and software components plus full assembly instructions.

bert
```                        Bert Supported by Scaffolding```

***
## Table of Contents 
  * [Hardware](#hardware)
    * [Skeleton](#skeleton)
    * [Joints](#joints)
    * [Tablet](#tablet)
  * [System Setup](#system)
    * [Android](#androidprep)
    * [Odroid](#odroid)
  * [Software Development](#software)
    * [IntelliJ](#intellij)
    * [Android Studio](#android)
    * [Other Tools](#other)
***
## Hardware 
Details of the hardware assembly are documented in [The Assembly Guild for the Poppy_Humanoid](https://docs.poppy-project.org/en/assembly-guides/poppy-humanoid)

### Skeleton 
[toc](#table-of-contents)

The skeletal print-files provided by GenerationRobots are in .STL format. This form is printable directly, but not conducive to modification.

![Bert Skeleton](/images/skeletal_assembly.png)
```                  Newly Assembled Skeleton     ```

Excellent assembly instructions may be found [here](https://github.com/poppy-project/poppy-humanoid/blob/master/hardware/doc/en/assemblyGuide.md). The
videos include step-by-step procedures for each motor group.
The following sections contain describe modifications we've made to the original instructions, if any.

#### Legs 
US child-size 8 shoes seem to fit. I used a 3D print coating, [XTC-3D](https://www.smooth-on.com/products/xtc-3d/) to effect a smooth, shiny finish on the feet.

#### Arms 
The hands are coated in [UreCoat](https://www.smooth-on.com/product-line/urecoat/) which gives a rather creepy-feeling soft latex covering. A flesh-toned [colorant](https://www.smooth-on.com/category/color-and-fillers/) was mixed into the coating before application.

#### Torso 
We used 2.5 x 12mm screws to fasten the 2 SMPS2Dynamixel boards to the torso. The video shows sticking them on with hot-glue.

We applied 12V power to each SMPS2Dynamixel separately from our power supply. There is no connection between SMPS2Dynamixel boards on the RS485 ports as shown in the assembly video. The RS485 port from the upper SMPs2Dynamixel board is used to power the 12V Odroid board.

We found that the hip y joints opened too far when there was no power applied. This resulted in tangled legs that interfered with each other causing excess stress on the wiring and serial connection errors.
Rubber bungee cords are used to bring the legs to a parallel position at rest.

![Leg Supports](/images/bungee.jpg)
```                  Flexible Leg Supports     ```

#### Head 
The head design was revised in our latest version to accommodate the Odroid N2+ processor.
In the photos, the revised head is gold in color.  

A frontal view of the skull:
![Skull Front](/images/revised_head_front.jpeg)
```                  Skull Front View     ```

A back view of the skull before cabling is attached :
![Skull Back](/images/revised_head_back_unplugged.jpg)
```                  Skull Back View     ```

The umbilical cable bundle extends from the rear-end of the head to torso. It includes:
 * 12V cable for power to Odroid
 * USB extension bundle for USB2Serial
 * HDMI 8" extension to save wear and tear on Odroid HDMI port

Here are two views of the bundle from the back:
 ![Umbilical undle1](/images/umbilical1.png)
 ```                  Processor Connections     ```

 ![Umbilical undle2](/images/umbilical2.jpg)
 ```                  Umbilical Bundle     ```

 And finally we show the back view with cabling attached and dongles inserted :
 ![Skull Back Wired](/images/revised_head_back.jpeg)
 ```                  Skull Back View     ```

#### Power Supply 
12V power for the Odroid processor is supplied directly through a custom cable. Note that
the outermost wire is connected to the outside sheath of the power connector.

![12V Processor Power](/images/12V_power_cord.png)
```                  12V Processor Power     ```

The main power pack, shown below, is constructed from a 3D-printed box (source code included). Inside it contains 2 AC/12V DC converters. The 12V connectors plug directly into the back of the robot.

![Power Supply](/images/power_supply.png)
```                  12V DC Power     ```

![Power Supply Mounted](/images/power_supply_mounted.png)
```                  Power Supply Mount     ```

### Joints 
[toc](#table-of-contents)

The [pypot](#pypot) python package must be installed on the Odroid to configure and test the Dynamixel motors.

The Dynamixel setup for flashing EEPROM is shown below:

![poppy](/images/dynamixel_configuration.png)
```                        Dynamixel Flashing Setup```

More detailed information may be found [here](https://docs.poppy-project.org/en/assembly-guides/poppy-torso/addressing_dynamixe)
```
python3 /usr/local/lib/python3.10/dist-packages/pypot/tools/dxlconfig.py
```
Initially, the devices can be found with the following parameters:
```
    Port:       /dev/tty/ACM0
    Protocol:   MX
    USB Device: USB2AX
    Baud rate:  57600
    ID       :  1
```

<em> Note: When the motors were fresh from the manufacturer, I used Robotis [Dynamixel Wizard](http://www.robotis.us/roboplus1) on a Windows machine to make the initial ID and baudrate settings.  Once a motor is configured, use ``dxl_write`` for further setup.</em>

In the motor EEPROM and RAM configuration, angles are defined such that 0 deg is at the bottom when viewing the front of the motor, 180 deg is to the top. Values decrease going clock-wise. Thus, for our purposes, decreasing values of position, load and speed all refer to the clock-wise direction.
Refer to the worksheet in the *git* repository at ``cad/DynamixelConfiguration.ods`` to find id and angle limit settings for each motor. In each case, set the baud rate to 1000000 and return delay time to 0.

In order to correct for a consistent user-view of position, joints may be corrected for orientation and given a fixed offset. A joint configured as *indirect* might be considered as if viewed from the back-side. The corrections give the following meanings to angular positions. These definitions should apply equally to joints on both sides of the body.

| Axis | <center>Description</center> |
| :--: | :---------------------- |
| x | Front-to-back |
| y | Side-to-side |
| z | Vertical |

| Joint | <center>Definition</center> | Min Angle | Max Angle |
| :------ | :--------------------------------------------------- | --------: | ---------: |
| Abs(x) | Angle of side-to-side bend of the torso. 180 is straight, lower values are to the right. | 150 | 210 |
| Abs(y) | Angle between the torso and pelvis, front-to-back, measured frontwards. | 150 | 210 |
| Abs(z) | Angle of twist in the torso. Zero is no twist. Positive is toward the right. | 45 | 45 |
| Ankle | Angle between the bottom of the foot and shin, frontwards.| 45 | 180 |
| Arm(z) | Degrees of twist of upper arm. Zero is straight ahead with the palm inward. Positive is outward. | -45 | 45 |
| Bust(x) | Angle of side-to-side bend of the upper body. 180 is straight, lower values are to the right. | 150 | 210 |
| Bust(y) | Angle between the chest and torso, front-to-back, measured toward the front. | 150 | 210 |
| Elbow | Angle between the upper and lower arms, measured frontwards. | 45 | 180 |
| Hip(x) | Angle of spread of thighs. 180 is straight down, decreases as the spread increases. | 155 | 205 |
| Hip(y) | Angle between the torso and thigh, in front. 180 is straight, 90 is forward, horizontal. | 75 | 225 |
| Hip(z) | Twist of leg with respect to torso. Zero is straight ahead. Negative is knock-kneed. | -45 | 20 |
| Knee | Angle between the thigh and lower leg, measured toward the back. | 50 | 180 |
| Neck(y)| Degrees the head is tipped. 0 is horizontal, positive is up. |-5|20|
| Neck(z)| Angle the head is facing. 0 is straight ahead, positive to the right. |-45|45|
| Shoulder(x) | Angle of spread of the arms. 180 is straight down, 90 is straight out to the side. | 90 | 215 |
| Shoulder(y) | Angle between the upper arm and chest. 180 is straight down, 90 is forward, horizontal. | 0 | 225 |
<center>``Angular Position Definitions``                     </center>

## System Setup <a id="system"/>
### Android 
[toc](#table-of-contents)

##### Persistent Storage
Configuration parameters, vocabulary and other data that are meant to be stored long-term reside in a SQLite database accessible through the tablet application.
Run the following scripts in order to prepare a SQLite database on the MacOSX development system to be accessible when running the Android Studio simulator with Android production code. In the
source ``install`` directory:

``./android_dev_data_dir.sh``
``./android_dev_db_setup.sh``

Note that the system must be restarted after the
first script.

##### Transfer to Tablet
In order for the application to be transferred to the tablet from the build system, the tablet must be connected via USB. Use the same USB cable that is used to charge the device.

The tablet must also be set in "developer" mode. This is accomplished under Settings->About Tablet->Software Information. Tap on "Build number" 7 times. (Yes, really). Under Settings->Developer options, enable USB debugging. Once the cable is connected a dialog should popup asking you to allow file transfer. (If this does not appear, you may have to fiddle with Developer options->USB Configuration).

On the build system, configure Android Studio (Tools->Run>Edit Configurations) to target the build output directly to a USB device. After a successful build, merely select the "run" button to transfer the **apk** executable to the tablet.

#### Tablet 

The tablet is a 12" Samsung Galaxy S8 running Android 13.0, API level 33. Android was chosen for its
speech capabilities. All speech analysis is done on the tablet hosting both text-to-speech and a speech
recognizer. At one time the tablet become stuck in headset mode. As a workaround, we bought an external
speaker that can ultimately be located in the head.

Make sure to update the language packages (Settings->General management->Language packs) and Google Speech Recognition and Synthesis application. The application is configured to speak English with a British accent. The voice is female (I'd prefer male).

### Odroid 
[toc](#table-of-contents)

##### Initial Configuration
The following sections describe setup of the main processor on the robot, an Odroid-N2+ running Linux, described [here](https://wiki.odroid.com/odroid-n2/odroid-n2). The initial board setup used an eMMC preloaded with Ubuntu Mate 22.04 purchased directly from [HardKernel](https://www.hardkernel.com/product-category/memories. Installation was very straightforward.

Unfortunately during an upgrade to Ubuntu 4.9.1, due to a supposed error in the kernel, we lost our wi-fi driver, effectively isolating the robot system and making it useless. To recover, we downloaded the image from [here](https://wiki.odroid.com/getting_started/os_installation_guide#operating_systems_we_re_providing), then flashed using `balenaEtcher` and an eMMC Reader board per instructions [here](https://linuxhint.com/etcher-image-writer-ubuntu-burn-images/). The Ubuntu desktop versions with Mate refused to copy to our eMMC (too big?). However the Ubuntu 22.04-4.9-minimal-odroid-n2 image flashed successfully. The text below describes setup from the minimal configuration.   

The N2 has 4 USB slots that are used for:
 * Keyboard/Mouse
 * WiFi
 * Bluetooth
 * USB2AX (2)

If the boot selector switch is to the left, startup will boot into Pettiboot. To boot from the SD card, move the switch to the right. The filesystems are pre-configured with the root at 64gb, 96% free. Place all user directories under `/home`.

#### Users
The initial root password is `root/odroid`. Change password to provide some minimal security. As `root` add an administrative user `odroid/odroid`.
Create a user for the robot's use . Call it `bert`. Add these to the `sudo`, `dialout` and `uucp` groups. For example:
```
   adduser bert
   usermod -aG sudo bert
   mkdir /home/bert/robot
   mkdir /home/bert/robot/src
```
Add the following to ``~/.bashrc`` and equivalent to ``~/Library/LaunchAgents/environment.plist``:
```
   PS1="\u: "
   export BERT_HOME=/home/bert
   export ROBOT_HOME=/home/bert/robot
   export JAVA_HOME=/usr/lib/jvm/java-11-openjdk-armhf
   export PATH=${PATH}:${BERT_HOME}/bin:${BERT_HOME}/.local/bin:${JAVA_HOME}/bin
```
#### Initial Network
The wi-fi connection must be configured before any additional packages can be installed. Our wireless interface is `wlan0`. The command
```
   nmcli device wifi connect "SSID" password "PASSWD"
```
should result in a wireless connection to the internet. (Substituting name and password for the local network,
of course). A reboot may be required. As soon as the network was live, I was presented with an invitation to upgrate to release 24.04.1. I proceeded with the upgrade, only to once again lose the wifi and had to start over again. The lesson here is to avoid the temptation to upgrade to 24.04.1.

Once a WiFi connection has been made, again as `root`,
```
  apt update
  apt upgrade -y
```

then install the `Budgie` desktop. The use of `aptitude` is required because of a dependency issue (which appeared common to all desktops I tried).
```
  add-apt-repository ppa:deadsnakes/ppa
  apt install aptitude
  aptitude install ubuntu-budgie-desktop
  apt install nautilus gnome-terminal
  shutdown -r now

```
If starting from a purchased SD card, remove the `Mate` desktop.
```
  apt purge mate-desktop --autoremove
```

#### Further Configuration

Now that a wi-fi connection is established and desktop installed, continue the configuration tasks that are required even with the pre-looaded SD card.

Set the hostname to `bert`.
```
  hostnamectl set-hostname bert
```

Set the timezone:
```
  timedatectl set-timezone America/Denver
```

 Configure a static IP address. This allows us to connect to the robot even if it comes up "headless". Using the Budgie desktop, under the main menu network icon, Network Settings, edit the WiFi connection via settings icon. On the IPV4 tab, change the Method: to "Manual". Add a static address, e.g. 10.0.0.42; 255.255.255.0; 10.0.0.1. Depending on the network, another common address choice might be: 192.168.1.42. In the same dialog, set Domain Name Servers, comma-separated.
```
  75.75.75.75
  75.75.76.76
```
Validate these setting by inspecting another machine on the same network.

Restart the `odroid`. When running again,
make sure you can ping the new address from a different machine.

Next, make sure these lines exist in `/etc/ssh/sshd_config`.
```
PubkeyAuthentication yes
AuthorizedKeysFile .ssh/authorized_keys
```

Then on each development system on the network, generate SSH keys (if not already done).
```
  ssh-keygen  (use default location, no password)
```
Also on each remote system, add to `/etc/hosts`:
```
  10.0.0.42 bert
```
Also on each remote system (appropriately replacing the username),
```
  cd ~/.ssh
  ssh-copy-id -i id_rsa.pub bert@bert
```
If there are old references to `bert` in *known_hosts*, they must be deleted.

Upgrade the operating system for any changes since the image was posted and install missing tools. If these *apt* commands repeatedly throw your wi-fi router off-line, you may be forced to execute them using a direct ethernet connection. These must be run as root (or sudo).

In the `Software Sources` application, enable main (canonical free and open source software)
```
  apt update
  apt upgrade -y
  apt autoremove -y
  apt autoclean -y
  apt install rsync
  apt install sqlite3
  apt install libjssc-java
  apt install libbluetooth-dev
  apt install build-essential
  apt-get install manpages-dev
```
```
   add-apt-repository ppa:xtradeb/apps -y
   apt update
   apt upgrade
   apt install chromium
   apt install firefox
```

As super-user, set the serial port permissions by creating file `/etc/udev/rules.d/50-ttyusb.rules` with the following contents:
```
KERNEL="ttyACM*",MODE="0666"
```
Reboot then as root:
```
  chmod 666 /dev/ttyACM*
``

In `/etc/ld.so.conf.d`, add a file named `bert.conf` containing the single line:
```
  /home/bert/robot/lib
```

Edit `/lib/systemd/system/bluetooth.service`
Replace the existing similar line with:
```
   ExecStart=/usr/lib/bluetooth/bluetoothd -C
```

To shutdown,
```
  shutdown -h now
```
Wait until the blue LED has gone out, then unplug.

##### Java
The Java JVM is used to run the application even though it is written in Kotlin. Download the latest Java Development (JDK) version using:
```
  apt update
  apt install openjdk-18-jre-headless
```
Installing the JDK allows us to compile on the Odroid, if necessary. Of course,
we also need the runtime. The java version on the odroid (18) must match the JDK on the development system.

Once the build has been executed on the Development system (and deployed), edit ``/etc/environment``, adding JAVA_HOME and BERT_HOME/bin to the **PATH** variable (before  */usr/bin*):
```
  /usr/lib/jvm/java-18-openjdk-arm64
  /home/bert/bin
```

#### PyPot 
*PyPot* provides demonstration code and the **herborist** tool that is used to configure Dynamixel stepper motors. Motors must be assigned unique IDs before being made part of the robot. ID's are recorded in `bert.xml`. Documentation may be found [here](https://github.com/poppy-project/herborist).
```
  sudo apt-get install python3-pip
  sudo apt-get install python3-pyqt5
  pip install pypot
  pip install herborist
```

## Software Development <a id="software"/>

The development host is an iMac running OSX Sonoma (14.3.1). The code repository resides on this machine. Code is cross-compiled and downloaded onto the robot target over a WiFi connection. Here is a diagram that summarizes the flow of the build and major tools used:
  Build Plan
  ````                        Development Tools ````

Code is compiled and downloaded onto the robot target over a WiFi connection using *rsync*.

The iMac requires the same Java version as the Odroid (Java 18). It is downloadable from [here](https://www.oracle.com/java/technologies/javase/jdk18-archive-downloads.html). Make sure to download the JDK and install the “Development tools” into the default location (e.g. /usr/local/bin). Extend the system path to include this area. Avoid the temptation to download "the latest" as we need Java 10 for compatibility with the Odroid.

### IntelliJ 
[toc](#table-of-contents)

##### Installation
*IntelliJ* is a powerful Integrated Development Environment (IDE) for Java, and Kotlin from Jet Brains. It can be downloaded [here]( https://www.jetbrains.com/idea/download/?section=mac). Make sure to download the community edition which is completely free. At the time of this writing, the latest version is “2022.2.1”.
Start *IntelliJ* and point it to the root of the `git` repository. Once started choose `File/Upload All From Disk` to synchronize with the repository. An internet connection is required as all third party libraries will be downloaded directly from public repositories during the build. Use the build configuration `install` to perform a complete build.

Our *IntelliJ* environment makes use of the `ANTLR` and `Python` plugins. See the menu page *IntelliJ* `Idea/Settings` to load.

##### Projects
`Bert` is a multi-module project. Each code group is its own project as follows:
  - `bertApp`: This contains the main class for the "Bert" application. It also contains entry classes for stand-alone tests.
  - `buildSrc`: _IntelliJ_ executes this project first. It is used to define plugins with dependencies and repositories that are common to the remaining source modules.
  - `common`: _common_ code contains utility functions and constant definitions used throughout the application.
  - `command`: _command_ is the module that interfaces with the tablet to
  acquire command and request strings. It communicates these to the _Dispatcher_
  and obtains responses.
  - `configuration`: This area is a collection of files that configure the robot. These include: scripts for installing and running the SQL database for poses and actions.
  It contains XML hardware definitions with dimensions and connectivity information.
  - `control`: Parse the URDF file and apply various control algorithms.
  - `database`: This is a common area for interaction with the SQLite database.
  - `dispatcher`: The _dispatcher_ is the central module for handling commands,
  passing them along to the _Motor_ controllers and then forwarding results
  to the original requestor.
  - `motor`: Java code for control of the various servo motors on the robot. These are executed by the _dispatcher_ application.
  - `speech`: This project is the interface between the _command_ module and syntax parser.
  - `syntax`: This project holds the _ANTLR_ code which defines the recognized syntax of "natural
    language" request strings.
  - `terminal`: _terminal_ is a separate application for command-line control of the robot. It provides the same interface as the Android tablet except in a typed instead of spoken form.

When complete the project workspace should look like:
![IntelliJ Setup](/images/intellij_setup.png)
```                  IntelliJ Projects     ```

##### Gradle Scripts
`Gradle` is a build system which follows a "convention over configuration" style. Each project has its own Kotlin build script named `gradle-build.kts`.

##### Scripts
The *IntelliJ* `Configuration` project has a collection of *bash* scripts and other configuration files as described below. When the project is built these files will be properly placed into `$BERT_HOME` subdirectories. These scripts perform both installation and run-time functions.

`bin`
 - bert - Execute *bertApp* from the command line. This is meant to be run on the Odroid target system
 - bert-blueserver - Script to start and stop the bluetooth server
 - bert-server - Script for starting and stopping the *bert* robot code
 - clear_logs - Remove current log files in preparation for the next test sequence.
 - install_blueserver_init_scripts - Configure the scripts that start and stop the bluetooth server. Thus
 must be run as superuser
 - install_blueserver_init_scripts - Configure the scripts that start and stop the robot. Thus
 must be run as superuser
 - mkdatabase - Create the SQLite *bert.db* database on either development or deployment system
 - start_bert - Start the robot
 - stop_bert - Stop the robot
 - test_port - test the all the serial ports

`csv`
 - Pose.csv -

`etc`
 - bert.xml -      Robot properties including a list of all controllable joints
 - urdf.xml -      A complete description of the skeletal connectivity

`pylib`
 - testport.py - Command-line tool to test serial ports based on the "herborist" tool

`sbin`
- bertdev - Execute *bertApp* in offline mode (no bluetooth nor serial) for testing.
- deploy - copy executable and configuration files onto the Odroid target
- install_odroid_source - copy code that must be compiled on the Odroid from the development source area
- unpack_distribution - This script is executed as a final step by the build. It unpacks library *.jar* files from the build into a proper distribution directories development machine.

`sql`
- createTables.sql - SQL commands used by *mkdatabase* to create tables

##### ANTLR
*ANTLR* is a parsing framework used for understanding natural language. Use the plugin available from the
*IntelliJ* settings page.

##### Git
*git* is the source code control tool. For development the repository is checked out as:
```
git clone http://[token]@github.com/chuckcoughlin/bert.git bert
```
where [token] is the private user token for the repository.

##### Python
*Python* is required for the *herborist* Dynamixel configuration application. Use the plugin available from the
*IntelliJ* settings page.

##### Modularized Jar Files
A few of the jar files were not available as `gradle` dependencies or were built using a too-old version of Java. These were updated manually for Java10 module compatibility.

Thanks to [Michael Easter](https://github.com/codetojoy/easter_eggs_for_java_9/blob/master/egg_34_stack_overflow_47727869/run.sh) for the following example that shows how to modularize the ``Jackson`` jar files.
A local directory holding the class files is taken as the root directory. This example uses 3 original non-modularized *Jackson* jar files have been downloaded into ``jars`as the starting point. Modularized results will be stored into ``mods``. In this particular example the modules are inter-dependent. In simpler cases only the first third of these steps are applicable.
```
   ROOT=`pwd`
   jdeps --generate-module-info work jars/jackson-core-2.9.7.jar
   cp jars/jackson-core-2.9.7.jar mods/jackson-core.jar
   rm -rf classes
   mkdir classes
   cd classes
   jar -xf ${ROOT}/jars/jackson-core-2.9.7.jar
   cd ${ROOT}/work/com.fasterxml.jackson.core
   javac -p jackson.core -d ${ARCHIVE}/classes module-info.java
   jar -uf ${ROOT}/mods/jackson-core.jar -C ${ROOT}/classes module-info.class

   cd $ROOT
   jdeps --generate-module-info work jars/jackson-annotations-2.9.7.jar
   cp jars/jackson-annotations-2.9.7.jar mods/jackson-annotations.jar
   rm -rf classes
   mkdir classes
   cd classes
   jar -xf ${ROOT}/jars/jackson-annotations-2.9.7.jar
   cd ${ROOT}/work/com.fasterxml.jackson.annotation
   javac -p jackson.annotations -d ${ROOT}/classes module-info.java
   jar -uf ${ROOT}/mods/jackson-annotations.jar -C ${ROOT}/classes module-info.class

   cd $ROOT
   jdeps --module-path ${generationrobots}/mods --add-modules com.fasterxml.jackson.annotation,com.fasterxml.jackson.core --generate-module-info work jars/jackson-databind-2.9.7.jar
   cp jars/jackson-databind-2.9.7.jar mods/jackson-databind.jar
   rm -rf classes
   mkdir classes
   cd classes
   jar -xf ${ROOT}/jars/jackson-databind-2.9.7.jar
   cd ${ROOT}/work/com.fasterxml.jackson.databin
   javac --module-path ${ARCHIVE}/mods --add-modules com.fasterxml.jackson.annotation,com.fasterxml.jackson.core -d ${ARCHIVE}/classes module-info.java
   jar -uf ${ROOT}/mods/jackson-databind.jar -C ${ROOT}/classes module-info.class
   ${ROOT}
   rm -rf work classes
```

### Android Studio 
[toc](#table-of-contents)

##### General
The tablet application, ***BertSpeak*** is the only Human Machine Interface (HMI) in normal operation.  Most importantly, it receives and analyzes voice commands, forming the only control interface. Additionally it maintains the voice transcript and displays results from the robot's internal health monitor. The tablet is a Samsung Galaxy Tab S8+, SM-X800, 10" Android 13 (SDK version 33).

The control application is a standard Android application built using Android Studio 3.4. (The studio may be downloaded from http://developer.android.com.) The studio requires a minor configuration of the host build system. Make the Android home environment variable available by adding to ~/.bashrc

    ```ANDROID_HOME=~/Library/Androd/sdk```

The password to the application keystore is: ```Andr0id```

##### Voice Commands
Voice commands are implemented purely via the Android tablet using the builtin speech-to-text features of Android. On the tablet, the ***BertSpeak*** app must be given microphone permissions.

For production of speech from robot output,  text-to-speech can be configured in the settings under "Accessibility". Parameters include languages supported and characteristics of the speaker such as volume.

##### Network Configuration
Communication between the tablet and main robot processor is over Bluetooth. On the tablet's settings "Connections" page, make sure that bluetooth is enabled. Under "More Connection Settings", enable "Nearby device scanning". Network or device pairing selections are made from menus accessed from the main screen.

Pairing with the robot must be completed before the ***BertSpeak*** application is started. Pairing may be initiated either from the robot or the tablet.

Note that the emulator does not support Bluetooth and is, therefore, not available as a test tool.

#### Other Tools <a id="other"/>
We make use of the following freely-available applications:
  * [Atom](https://atom.en.softonic.com/mac) - Text editor, handles markdown syntax
  * [OpenSCAD](http://www.openscad.org) - Construct 3D CAD drawings in script. Export in .stl format. This is useful where the parts are composed from simple geometric shapes.
  * [MeshLab](http://www.meshlab.net) - Use this tool to optimize and convert between 3D formats.
  * [Blender](http://www.blender.org) - Create 3D models. Use `Blender-2.8` for modeling parts that are not part of the
  original `poppy` design. Export in .obj format for printing.
  * [pypot.dynamixel](https://poppy-project.github.io/pypot/dynamixel.html) - Configure Dynamixel servos using a command-line interface.
  * [Boxy](https://apps.apple.com/us/app/boxy-svg/id611658502) - Construct SVG diagrams and charts ($19.95).
  * [iCircuit](https://itunes.apple.com/us/app/icircuit/id454347770?ls=1&mt=12) - Draw and analyze electrical circuits.

##### Blender Cheat Sheet
*Blender* is a sophisticated (read complex)
modeling application. There are numerous
keyboard shortcuts that not at all obvious from the interface. Here are a few:
  * ctl-a - launch apply menu
  * D - duplicate selected object
  * L - link (ctl/shift)
  * g - enter mode for direct manipulation of objects. Follow with x,y,z,s or r. Exit with <ENTER>.
  * m - create collection of selected objects
  * n - expand the navigation widget to allow
  precise positioning of objects
  * r - rotate (after "g")
  * s - scale (after "g")
  * t - toggle left-side toolbar

##### Useful Commands I Always Forget

  To query the module in a jar file: `jar --file="<file>" --describe-module`

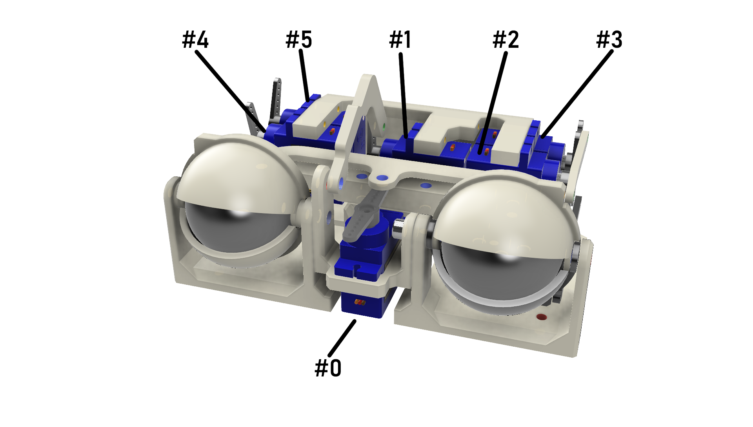
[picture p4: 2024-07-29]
cad/eyes/EyeMechanics/Reference/Servo numbers.png

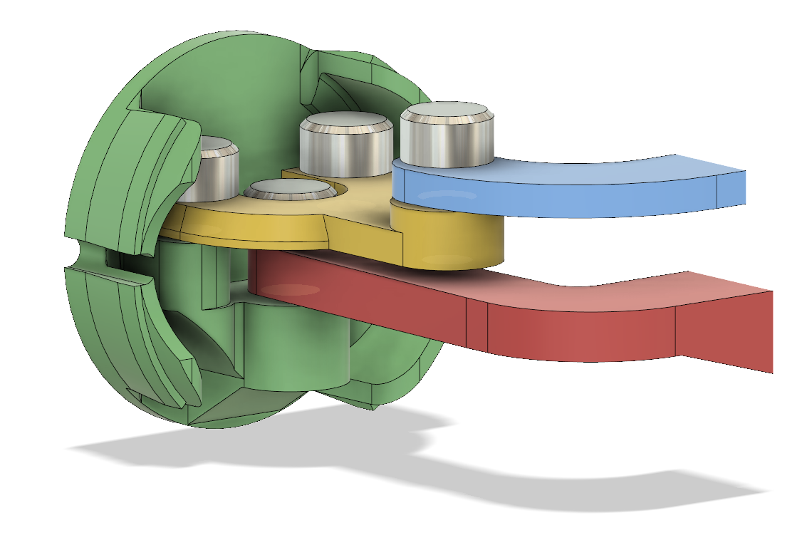
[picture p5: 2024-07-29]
cad/eyes/EyeMechanics/Reference/eye together.PNG

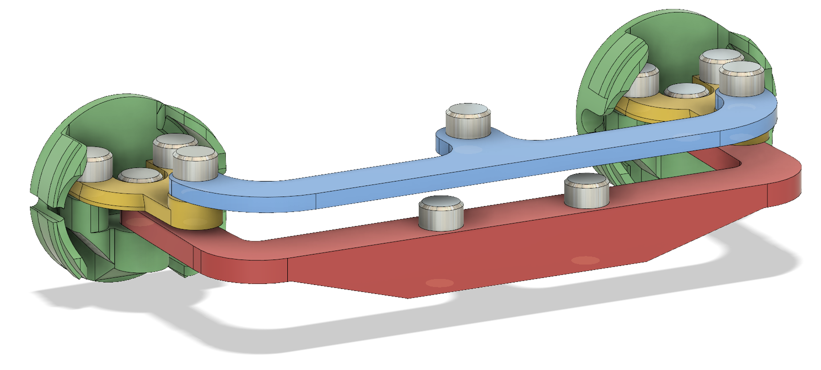
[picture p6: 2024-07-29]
cad/eyes/EyeMechanics/Reference/x axis.PNG

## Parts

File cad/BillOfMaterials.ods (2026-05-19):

 | Bill of Materials – humanoid v 1.0.2 – excludes shipping
 | https://github.com/poppy-project/poppy-humanoid/blob/master/hardware/doc/BOM.md
Description | Part Number | Supplier | Qty | Unit Cost | Total | Ordered | Received
Main processor – ARM – 8 core, 2Ghz, 2Gb, eMMC5.0 16-64Gb Flash Storage, passive heatsink,power connector | Odroid-N2+ | Hardkernel | 1 | 75.5 | 75.5 | 08/02/22 | 10/13/22 | Should have ordered with fan instead of heatsink
64Gb eMMC and Ubuntu Linux |  | Hardkernel | 1 | 29 | 29 | 08/17/23 | 08/25/23
Wifi Dongle | WiFi Module 3 | Hardkernel | 1 | 6 | 6 | 10/02/18 | 10/12/18
Bluetooth Dongle (USB) | CSR8510 | Hardkernel | 1 | 3.8 | 3.8 | 10/02/18 | 10/12/18
DC/DC Step-Down Converter – 5V | UBEC P1385A | AdaFruit | 2 | 9.95 | 19.9 | 01/25/19 | 02/02/19 | Power for Odroid
USB Keyboard and Mouse | Logitec MK235 | Office Max | 2 | 19.51 | 39.02 |  | 10/31/18
USB2AX – USB to serial | USB2AX | Generation Robots | 3 | 45 | 135 | 11/25/18 | 12/22/18 | Hard to find
USB 2 4-port hub | Insten 4-Port Octopus USB Hub | Quill | 1 | 7.49 | 7.49 | 01/25/19 | 02/04/19
MX64-AT Actuator | Dynamixel MX-64AT | Trossen Robotics | 4 | 309.9 | 1239.6 | 10/02/18 | 10/11/18
MX28-AT Actuator | Dynamixel MX-28AT | Trossen Robotics | 1 | 239.9 | 239.9 | 10/02/18 | 10/12/18
MX28-AT Actuator (6-pack) | Dynamixel MX-28AT | Trossen Robotics | 3 | 1199.5 | 3598.5 | 10/02/18 | 10/12/18
AX-12A Actuator | Dynamixel AX-12A | Trossen Robotics | 2 | 44.9 | 89.8 | 10/02/18 | 10/12/18
MX28 Servo Horn set | HN07-N101 | Trossen Robotics | 18 | 7.51 | 135.18 | 10/02/18 | 10/12/18
MX28 Servo Idler bearing set | HN07-i101 | Trossen Robotics | 12 | 14.1 | 169.2 | 10/02/18 | 10/12/18
MX64 Servo Horn set | HN105-N102 | Trossen Robotics | 0 | 10.9 | 0
MX64 Servo Idler bearing set | HN05-i101 | Trossen Robotics | 4 | 15.4 | 61.6 | 10/02/18 | 10/12/18
Wrench bolt M2*3 – 200 count | Wrench bolt M2*3(200) | Robotis | 1 | 13.9 | 13.9 | 10/04/18 | 10/12/18
Wrench bolt M2.5*4 – 200 count | Wrench bolt M2.5*4(200) | Robotis | 1 | 13.9 | 13.9 | 10/04/18 | 10/12/18
Wrench bolt M2.5*6 – 200 count | Wrench bolt M2.5*6(200) | Robotis | 1 | 13.9 | 13.9 | 10/04/18 | 10/12/18
Wrench bolt M2.5*8 – 200 count | Wrench bolt M2.5*8(200) | Robotis | 1 | 13.9 | 13.9 | 10/04/18 | 10/12/18
BIOLOID Bolt Nut Set | BNS-10 | Robotis | 1 | 23.4 | 23.4 | 10/04/18 | 10/12/18
Nut M2.5 – 400 | Nut M2.5 | Robotis | 1 | 3.9 | 3.9 | 10/04/18 | 10/12/18
N1 Nut M2 – 400 | N1 Nut M2 (400) | Robotis | 1 | 3.4 | 3.4 | 10/04/18 | 10/12/18
SMPS2Dynamixel | SMPS2Dynamixel | Robotis | 2 | 5.9 | 11.8 | 10/04/18 | 10/12/18
Power Supply | SMPS 12V 5A | Robotis | 1 | 29.9 | 29.9 | 10/04/18 | 10/12/18
3 Pin Extension PCB | 3P Extension PCB | Robotis | 3 | 2.9 | 8.7 | 10/04/18 | 10/12/18
3 Pin Cable 65mm – 10 count | CBL-BIO60 | Trossen Robotics | 1 | 10.9 | 10.9 | 10/02/18 | 10/12/18
3 Pin Cable 100mm – 10 count | CBL-BIO100 | Trossen Robotics | 1 | 11.9 | 11.9 | 10/02/18 | 10/12/18
3 Pin Cable 150mm – 10 count | RO-903-0076-000 | Trossen Robotics | 1 | 12.9 | 12.9 | 10/02/18 | 10/12/18
3 Pin Cable 200mm – 10 count | Dynamixel 200mm 3p cable (10) | Trossen Robotics | 1 | 13.9 | 13.9 | 10/02/18 | 10/12/18
3 Pin Cable 220mm – 3 count | (included below)
3 Pin Cable 250mm – 3 count | CBL-BIO250 (10) | Trossen Robotics | 1 | 14.9 | 14.9 | 10/02/18 | 10/12/18
3 Pin Cable 500mm | CBL-BIO500 | Trossen Robotics | 2 | 3.95 | 7.9 | 10/02/18 | 10/12/18
4 Pin Cable 200mm – 2 | Dynamixel 200mm 4p cable (10) | Trossen Robotics | 1 | 26.48 | 26.48 | 10/02/18 | 10/12/18
HDMI Extension Cable – 8in | HDMI Port Saver | Zoro | 1 | 4.05 | 4.05 | 01/25/19 | 01/29/19
Brass standoffs – 2.5mm x 16mm | 2337 | Adafruit | 8 | 0.625 | 5 | 07/14/24 | 07/20/24
Mini pan-tilt kit w/ micro servos | 1967 | Adafruit | 2 | 18.95 | 37.9 | 07/14/24 | 07/20/24
 |  |  |  |  | 0
Other:
Wireless keyboard and Mouse |  | NASR | 1 | 61.99 | 61.99 | 08/29/23 | 08/31/23
IMU – 3 axis accelerometer, gyros | 9DoF Razor IMU M0 | Sparkfun | 1 | 35.95 | 35.95 | 06/09/19 | 06/13/19
Stereo Amplifier – 3.7w | Max898306 | AdaFruit | 1 | 8.95 | 8.95
Mini USB 2.0 megapixel Webcam – 170 deg fov |  | ??
3D print of box to hold power supply – ABS, black |  | CraftCloud | 1 | 34.9 | 34.9 | 08/07/23 | 08/14/23
Android tablet* | Samsung Galaxy S3 – 10” | BestBuy | 1 | 495 | 495 | 10/01/17 | 10/01/17
Raspberry Pi 5 – 4 GB RAM* | 5812 | Adafruit | 1 | 60 | 60 | 07/14/24 | 07/20/24
16 channel PWM / Servo HAT for Raspberry Pi* | 2327 | Adafruit | 1 | 17.5 | 17.5 | 07/14/24 | 07/20/24
Supplier | URL |  |  | Total | 6846.31
AdaFruit | https://www.adafruit.com/
Amazon | https://www.amazon.com/
Generation Robots | https://www.generationrobots.com
Hardkernel | https://www.hardkernel.com
Quill | https://www.quill.com
Robotis | http://www.robotis.us
Sparkfun | https://www.sparkfun.com/
Trossen Robotics | https://www.trossenrobotics.com
Zoro | https://www.zoro.com
* not included in sale

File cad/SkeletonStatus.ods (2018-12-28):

 | Self-printed parts – humanoid v 1.0.2
 | https://github.com/poppy-project/poppy-humanoid/blob/master/hardware/doc/BOM.md
Group | Part Name | Qty | Printed | Source
Arms | ArmConnector | 2 | x | Library | Boulder Public Library – Makerspace
 | ForearmLeft | 1 | x | Friend
 | ForearmRight | 1 | x | Friend
 | HandLeft | 1 | x | Library
 | HandRight | 1 | x | Library
 | ShoulderLeft | 1 | x | Friend
 | ShoulderRight | 1 | x | Friend
 | UpperArm | 2 | x | Friend
Head | CameraSupport | 1
 | HeadBack | 1 | x | Friend
 | Face | 1 | x | Friend
 | Neck | 1 | x
 | ScreenSupport | 1
 | Screen | 1
 | SpeakerLeft | 1
 | SpeakerRight | 1 |  | Library
Legs | HipLeft | 1 | x | Library
 | HipRight | 1 | x | Library
 | HipZToHipYConnector | 2 |  | Friend
 | Pelvis | 1 | x | Friend
 | Shin | 2 | x | Friend
 | FootLeft | 1 | x | Library
 | FootRight | 1 | x | Library
 | ThighLeft | 1 | x | Friend
 | ThighRight | 1 | x | Friend
Trunk | Abdomen | 1 | x | Friend
 | Chest | 1 | x | Friend
 | i101ToMX28Link | 1 | x | Library
 | i101ToMX64Link | 1 | x | Library
 | MX28DoubleRotationLink | 2 | x | Library
 | MX64DoubleRotationLink | 2 | x | Library
 | Spine | 1 | x | Friend

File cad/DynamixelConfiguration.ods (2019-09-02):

 | Dynamixel Configuration
 |  |  |  | Target* | Target* | Actual** | Actual | Configured*** | Configured
Name | Type | ID | Offset**** | Min Angle | Max Angle | Min Angle | Max Angle | Min Angle | Max Angle | Orientation
ABS_X | MX-64 | 32 | 0 | -45 | 45 | 107 | 247 | 150 | 210 | direct
ABS_Y | MX-64 | 31 | 16 | -50 | 12 | 105 | 202 | 150 | 210 | direct
ABS_Z | MX-28 | 33 | -160 | -90 | 90 | 74 | 288 | -60 | 60 | direct
BUST_X | MX-28 | 35 | 5 | -40 | 40 | 123 | 243 | 150 | 210 | direct
BUST_Y | MX-28 | 34 | 24 | -67 | 27 | 95 | 229 | 150 | 210 | direct
NECK_Y | AX-12 | 37 | -120 | -45 | 6 | 114 | 168 | -5 | 20 | direct
NECK_Z | AX-12 | 36 | -150 | -90 | 90 | 58 | 239 | -30 | 30 | indirect
LEFT_ANKLE_Y | MX-28 | 15 | -91 | 135 | 225 | 108 | 244 | 60 | 135 | direct
LEFT_ARM_Z | MX-28 | 43 | -198 | -105 | 105 | 41 | 302 | -45 | 90 | indirect
LEFT_ELBOW_Y | MX-28 | 44 | 17 | -148 | 1 | 1 | 199 | 45 | 180 | direct
LEFT_HIP_X | MX-28 | 11 | -8 | -30 | 28.5 | 136 | 229 | 155 | 205 | indirect
LEFT_HIP_Y | MX-64 | 13 | -18 | -104 | 84 | 84 | 298 | 60 | 225 | direct
LEFT_HIP_Z | MX-28 | 12 | -200 | -25 | 90 | 62 | 228 | -45 | 20 | indirect
LEFT_KNEE_Y | MX-28 | 14 | -4 | -3.5 | 134 | 165 | 330 | 50 | 180 | indirect
LEFT_SHOULDER_X | MX-28 | 42 | -70 | -105 | 110 | 49 | 312 | 90 | 215 | direct
LEFT_SHOULDER_Y | MX-28 | 41 | -65 | -120 | 155 | 9 | 360 | 0 | 225 | direct
RIGHT_ANKLE_Y | MX-28 | 25 | -108 | 135 | 225 | 109 | 247 | 60 | 135 | indirect
RIGHT_ARM_Z | MX-28 | 53 | -180 | -105 | 105 | 57 | 311 | -45 | 90 | direct
RIGHT_ELBOW_Y | MX-28 | 54 | 4 | -1 | 148 | 163 | 351 | 45 | 180 | indirect
RIGHT_HIP_X | MX-28 | 21 | 16 | -28.5 | 30 | 107 | 238 | 155 | 205 | direct
RIGHT_HIP_Y | MX-64 | 23 | -18 | -85 | 105 | 84 | 298 | 60 | 225 | indirect
RIGHT_HIP_Z | MX-28 | 22 | -160 | -90 | 25 | 62 | 228 | -45 | 20 | direct
RIGHT_KNEE_Y | MX-28 | 24 | 15 | -134 | 3.5 | 6 | 186 | 50 | 180 | direct
RIGHT_SHOULDER_X | MX-28 | 52 | -105 | -110 | 105 | 40 | 305 | 90 | 215 | indirect
RIGHT_SHOULDER_Y | MX-28 | 51 | -100 | -155 | 120 | 0 | 323 | 0 | 225 | indirect
 | * Attempted min/max angle settings through “herborist” as specified in Poppy docs. Widget is not very precise. 180 is top, decreasing clock-wise.
 | ** As read from EEPROM. Actual “hard” limits enforced by firmware. Application limits may be more restrictive.
 | *** Limits as configured in the XML file. These are “soft” limits enforced by the application and take into account the offset, orientation and desired range of motion.
 | **** Fixed angular correction applied by the application, empirically derived

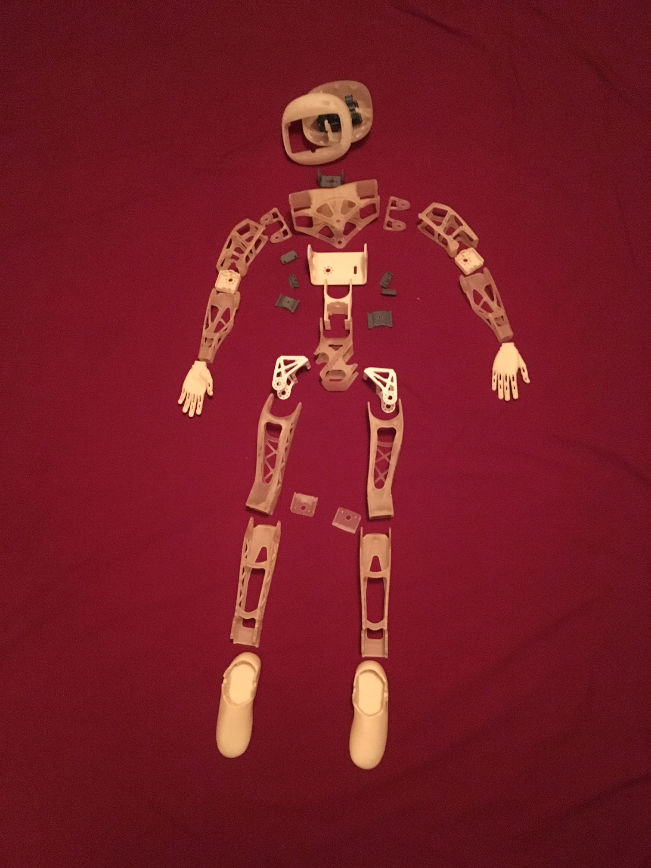
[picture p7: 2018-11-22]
images/printed_parts.jpg

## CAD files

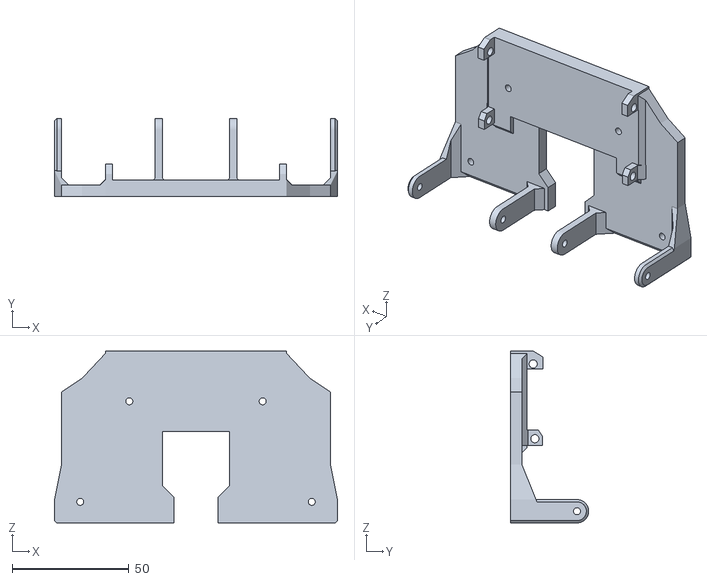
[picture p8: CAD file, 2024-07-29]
cad/eyes/EyeMechanics/stl/Main Base.stl
121.0 x 33.5 x 73.5

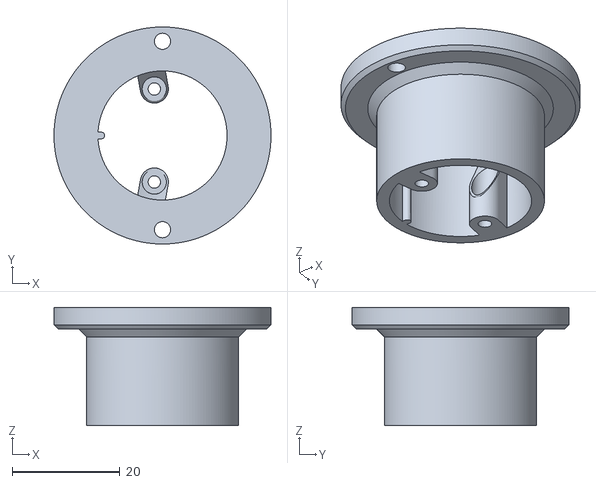
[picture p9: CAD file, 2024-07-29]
cad/eyes/EyeCasting/Casting Base.stl
40.3 x 40.3 x 22.0

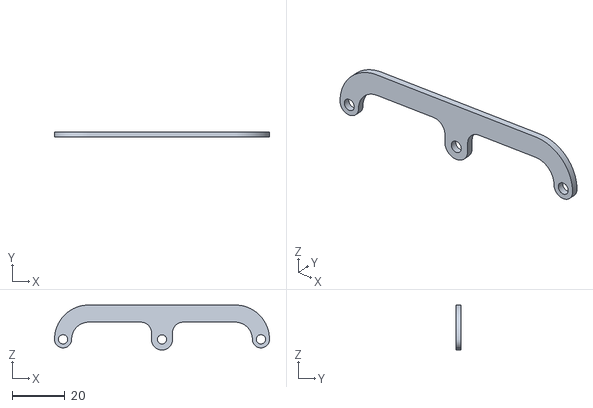
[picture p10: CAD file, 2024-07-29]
cad/eyes/EyeMechanics/stl/Three-Point Connector.stl
81.5 x 2.00 x 17.1

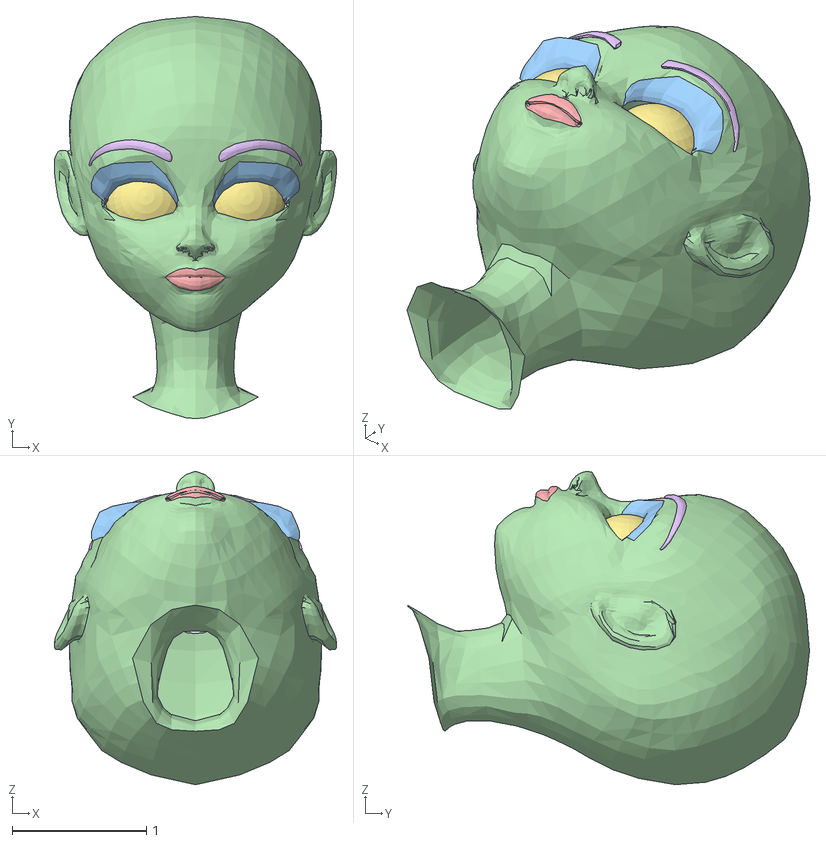
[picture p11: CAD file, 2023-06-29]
cad/face/cartoon_head.obj
2.11 x 3.00 x 2.34
cartoon_female_head_4460_4384_some_head_anatomy_girl_eyes.001_body_girl.003_Material.019
cartoon_female_head_4460_4384_some_head_anatomy_girl_eyes.001_body_girl.003_Material.017
cartoon_female_head_4460_4384_some_head_anatomy_girl_eyes.001_body_girl.003_Material.015
cartoon_female_head_4460_4384_some_head_anatomy_girl_eyes.001_body_girl.003_skin.007
cartoon_female_head_4460_4384_some_head_anatomy_girl_eyes.001_body_girl.003_Material.606
cartoon_female_head_4460_4384_some_head_anatomy_girl_eyes.001_body_girl.003_Material.514
cartoon_female_head_4460_4384_some_head_anatomy_girl_eyes.001_body_girl.003_Material.513

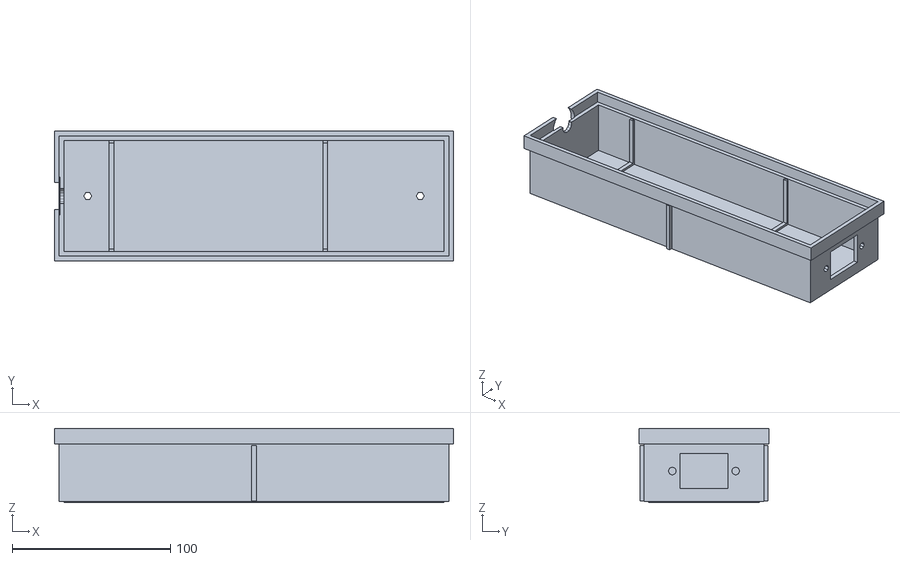
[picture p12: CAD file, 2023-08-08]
cad/powerbox/bottom.stl
252.0 x 82.0 x 47.0

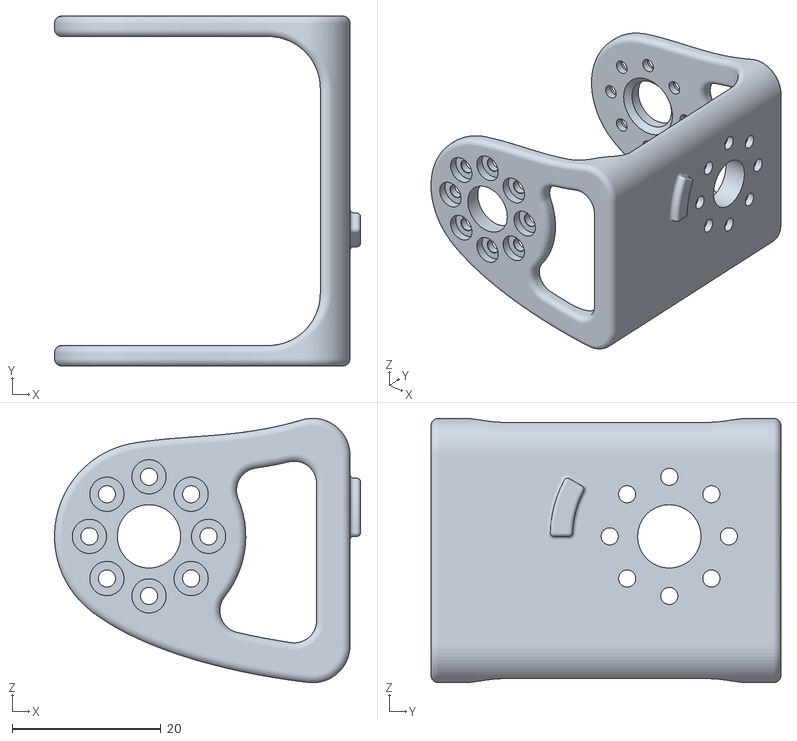
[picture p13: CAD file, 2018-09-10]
cad/skeleton/arms/shoulder_right.STL
41.1 x 47.0 x 35.5

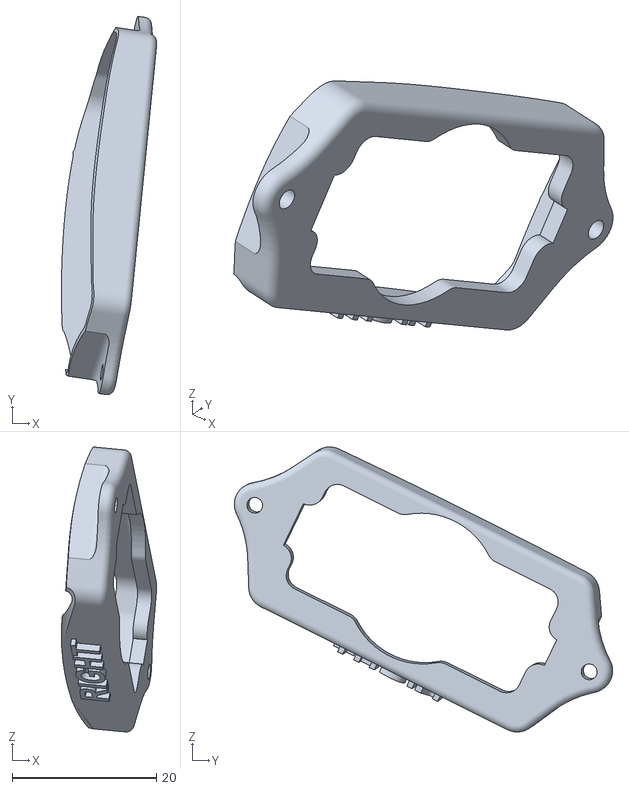
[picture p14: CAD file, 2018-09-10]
cad/skeleton/head/speaker_right.STL
13.2 x 52.4 x 39.5

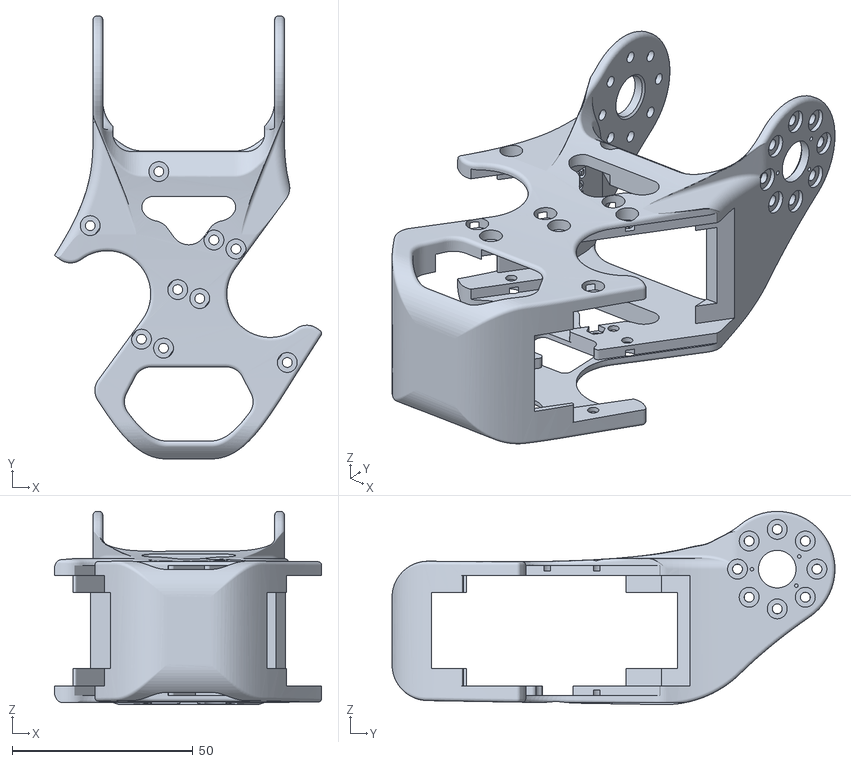
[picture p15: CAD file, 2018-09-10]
cad/skeleton/legs/pelvis.STL
74.0 x 122.7 x 53.5

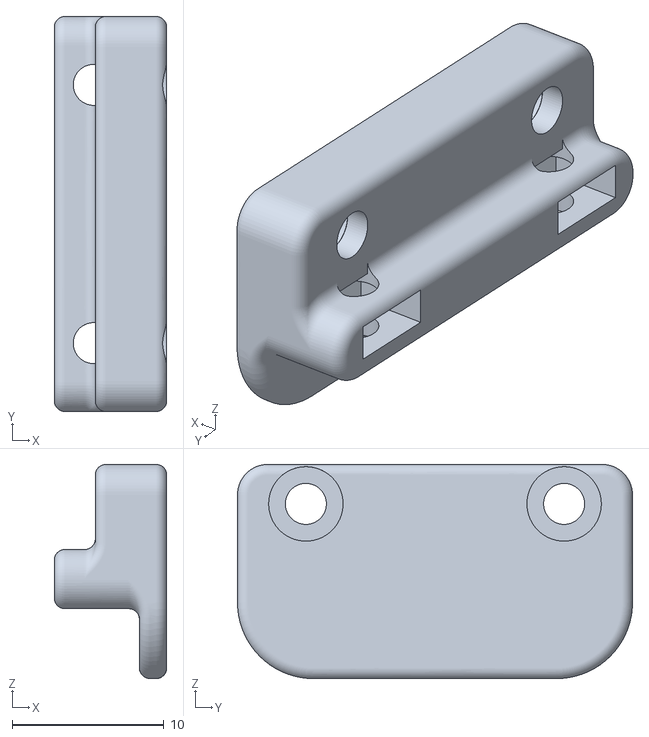
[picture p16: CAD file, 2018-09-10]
cad/skeleton/trunk/MX28_double_rotation_link.STL
7.40 x 26.0 x 14.1

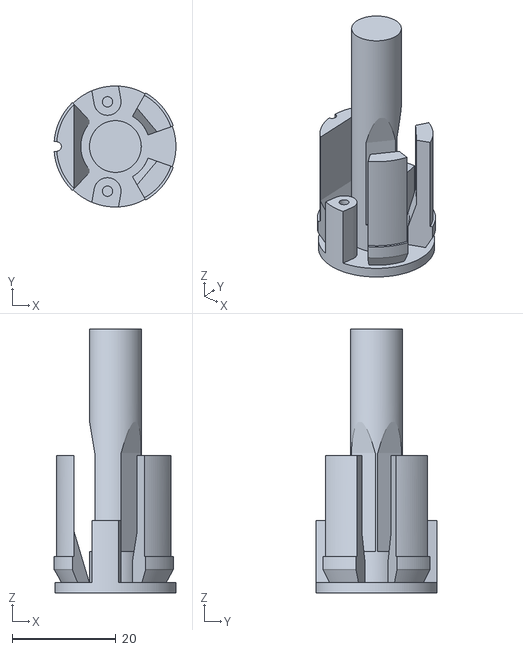
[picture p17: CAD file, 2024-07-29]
cad/eyes/EyeCasting/Painting Snap-Fit.stl
23.5 x 23.4 x 51.0

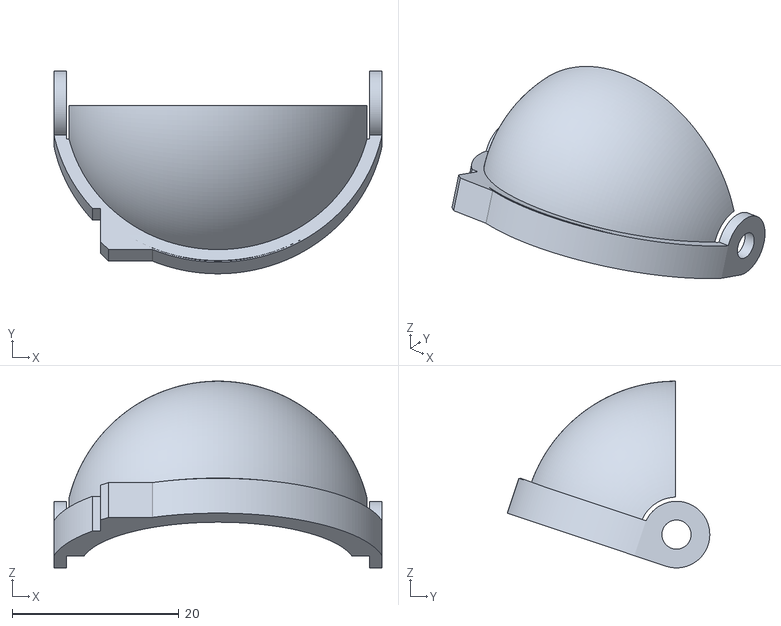
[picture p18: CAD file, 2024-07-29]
cad/eyes/EyeMechanics/stl/Bottom Right Lid.stl
39.4 x 24.3 x 22.4

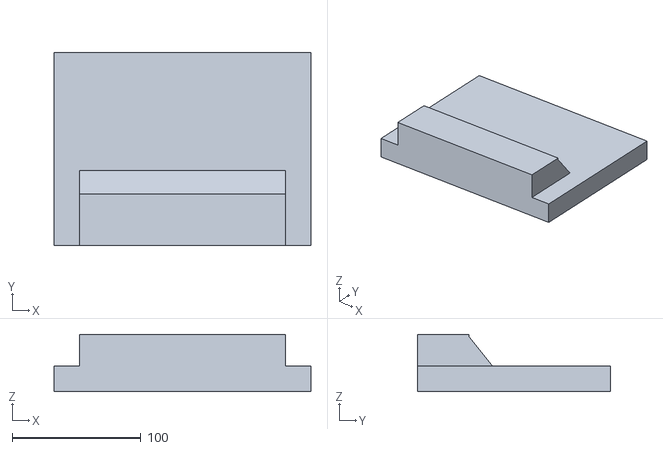
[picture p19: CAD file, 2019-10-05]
cad/face/blocks.stl
200.0 x 150.0 x 44.5

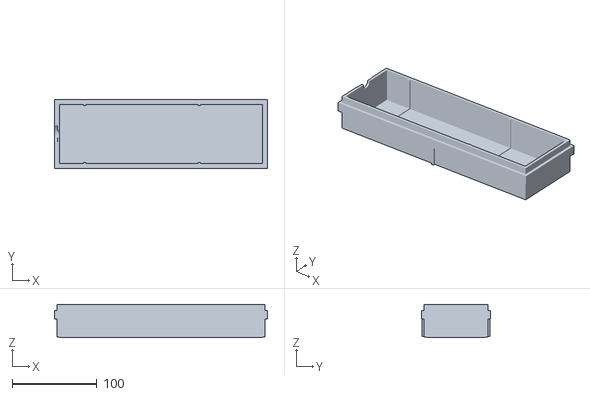
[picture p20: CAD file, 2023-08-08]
cad/powerbox/top.stl
252.0 x 82.0 x 39.2

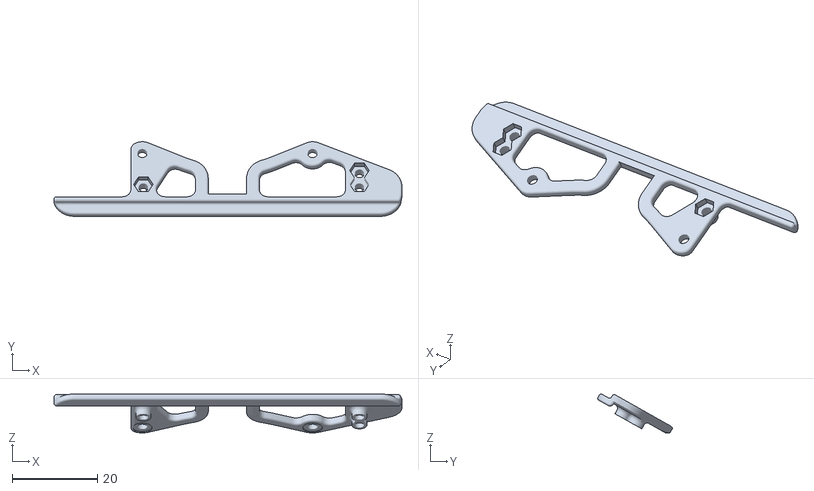
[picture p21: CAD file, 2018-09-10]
cad/skeleton/head/camera_support.STL
81.7 x 17.5 x 9.15

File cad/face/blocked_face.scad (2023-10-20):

// Import the Poppy face model. Use simple shapes to cut out the actual face,
// leaving only the collar which screws into the back of the head.

// Load the face
module load_stl() {
 import("face_raw.stl");
}

module base() {
    translate([0,0,-18]) {
        cube( size=[200,150,20],center=true);
    }
}

// Use a triangular prism to block out the neck area.
module prism() {
    
 translate([80,-16,16]) {
 rotate([0,90,180]) {
     linear_extrude(height=160) {
    polygon([[25,20],[0,20],[25,0]]);
 }}}
}
module neck() {
    translate([0,-55,4]) {
        cube( size=[160,40,25],center=true);
    }
}
union() {
    load_stl();
    base();
    prism();
    neck();
}

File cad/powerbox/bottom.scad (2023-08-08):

// OpenSCAD for the bottom of a box to hold the power supplies
//          110V 60hz to 12V conversion for Bert
//          Origin = center, bottom of bottom plate

height    = 37;        // Inside height (1/2 high)
length    =240;        // Inside length
rib_thickness = 3;     // Thickness of ribs and other supports
thickness =  3;        // Wall and bottom thickness
width     = 70;        // Inside width

// Bottom plate. 
// x = length
// y = width
module base(x,y) {
    $fn=100;
    linear_extrude(thickness,center=true,convexity=10) {
       square([x,y],center=true); 
    }
}

module end(y,z) {
   linear_extrude(thickness,center=true,convexity=10) {
       square([y,z],center=true); 
    } 
}
module side(x,z) {
   linear_extrude(thickness,center=true,convexity=10) {
       square([x,z],center=true); 
    } 
}

module ac_wire_opening() {
    screw_separation = 40; // center-center between screws
    screw_radius = 2.5;    // screw hole in socket
    // Dimension C-13 female plug socket
    plug_height = 22;  // Socket height
    plug_width  = 30;  // Socket width
    plug_top_edge=16;
    
    // Rectangle
    linear_extrude(thickness+1,center=true,convexity=10) {
       polygon([[-plug_width/2,plug_height/2],
                [plug_width/2,plug_height/2],
                [plug_width/2,-plug_height/2],
                [-plug_width/2,-plug_height/2]]); 
    } 
    translate([screw_separation/2,0,0])
    cylinder(thickness+1,screw_radius,screw_radius,true);
    translate([-screw_separation/2,0,0])
    cylinder(thickness+1,screw_radius,screw_radius,true);
}
// Material to be added to top edge so cover fits. Outside edge.
// Arguments are the length and with of the band.
module band(x,w) {
    z = rib_thickness;
    linear_extrude(height=x,center=true,convexity=10) {
        square([z,w],center=true); 
    }
}
module bottom_screw_holes(x) {
    dx = 15;           // Screw hole offset from end
    sr = 2.5;          // Radius for screw hole
    translate([x/2-dx,0,0])
    cylinder(thickness+1,sr,sr,true,$fn=6);
    translate([dx-x/2,0,0])
    cylinder(thickness+1,sr,sr,true,$fn=6);
}
// Half circle opening
module dc_grommet_opening(z) {
    wr  = 12;    // Grommet radius for 12V wires
    translate([0,z/2,0])
    cylinder(thickness+1,wr,wr,true);
}
// Half circle opening
module dc_wire_opening(z) {
    wr  = 5;    // Washer radius for 12V wires
    translate([0,z/2,0])
    cylinder(thickness+1,wr,wr,true);
}
// The ribs help stiffen the sides and 
// hold the transformer in place. The argument is
// the length of the rib
module rib(h) {
    z = rib_thickness;
    linear_extrude(height=h,center=false,convexity=10) {
        square([z,z],center=true); 
    }
}

  
// -------- Final Assembly --------
module final_assembly(x,y,z) {
    // Bottom
    color("gray")
    translate([0,0,thickness/2])
    difference() {
        base(x,y);
        bottom_screw_holes(x);
    }
    
    // DC End
    rotate([90,0,90])
    translate([0,(z+thickness)/2,-(x+thickness)/2])
    difference() {
        union() {
            color("red")
            rotate([0,90,0])
            translate([thickness,z-15,0])
            band(y+2*thickness,10);
            color("lightgreen")
            end(y+2*thickness,z+thickness/2);
        }
        union() {
            dc_wire_opening(z);
            translate([0,0,-thickness])  // Only the "band"
            dc_grommet_opening(z);
        }
    }
    
    // AC End
    rotate([90,0,90])
    translate([0,(z+thickness)/2,(x+thickness)/2])
    union() {
        difference() {
                color("green")
            end(y+2*thickness,z+thickness/2);
            ac_wire_opening();
        }
        color("red")
        rotate([0,90,0])
        translate([-thickness,z-15,0])
        band(y+2*thickness,10);
    }
    
    // Side
    rotate([90,0,0])
    translate([0,(z+thickness)/2,(y+thickness)/2])
    union() {
        color("green")
        side(x,z+thickness/2);
        rotate([90,0,0])
        translate([0,thickness/2,thickness/2])
        band(y/2,5);
        rotate([0,90,0])
        translate([-thickness,z/2+5-thickness/2,0])
        band(x+4*thickness,10);
    }
    
    // Side
    rotate([90,0,0])
    translate([0,(z+thickness)/2,-(y+thickness)/2])
    union() {
        color("green")
        side(x,z+thickness/2);
        rotate([90,0,0])
        translate([0,-thickness/2,thickness/2])
        band(y/2,5);
        rotate([0,90,0])
        translate([thickness,z/2+5-thickness/2,0])
        band(x+4*thickness,10);
    }
    // Interior support
    union() { 
        color("black");
        offset = 30-length/2;
        translate([offset,width/2,thickness/2])
        rib(height);
        translate([offset,-width/2,thickness/2])
        rib(height);
        rotate([90,0,0])
        translate([offset,thickness,-width/2])
        rib(width);
        
    }
    union() { 
        color("red");
        offset = length/2-75;
        translate([offset,width/2,thickness/2])
        rib(height);
        translate([offset,-width/2,thickness/2])
        rib(height);
        rotate([90,0,0])
        translate([offset,thickness,-width/2])
        rib(width);  
    }
}

final_assembly(length,width,height);

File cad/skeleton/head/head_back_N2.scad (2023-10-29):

// Modify the original Poppy head_back to accomodate
// the Odroid-N2 computer board. 
brd_height = 30; 
brd_length = 90;     // Circuit board length
brd_width  = 90;     // Circuit board length
back_offset  = 500;    // Origin to back of head
offset_x=-0;  
offset_y=-320;
offset_z=0;
// Place skull in center, align to axes
// x to sides, y forward and back, z is top and bottom
// Offsets make origin in center of head
module load_stl() {
    color("gray")
    rotate([125,0,0])
    translate([offset_x,offset_y,offset_z]) {
        import(file="head_back.STL",convexity=5);
    }
}

// Use this box to clear back-side and a grove along the rail
module back_opening() {
    color("green");
    union() {
    translate([0,50,20]) {   // x,  ,   
        cube([brd_width,40,brd_height],true);
    }
    translate([brd_width/2+2,30,17]) { // right groove
      cube([4,brd_length,20],true);     
    }
    translate([-brd_width/2-2,30,17]) { // left groove
      cube([4,brd_length,20],true);
    }
    translate([brd_width/2+4,30,21]) { // tiny groove right
      cube([2,brd_length,5],true);
    }
    translate([-brd_width/2-4,30,21]) { // tiny groove left
      cube([2,brd_length,5],true);
    }
  }
}

// Rack to hold the printed circuit board
module rack(){
    w  = 10;   // Rail width
    t1 = 6;    // Rail thickness
    t2 = 4;    // Cross piece thickness
    difference() {
      union() {
       // Left rail 
       translate([brd_width/2-w/2,23,t1+t2]) {
         cube([w,brd_length,6],true);
       }
       // Right rail 
       translate([-brd_width/2+w/2,23,t1+t2]) {
         cube([w,brd_length,6],true);
       }
       // Back rail 
       translate([0,brd_length/2,t2+1]) {
         cube([brd_width,w,t2],true);
       }
       // Far back rail
       translate([0,brd_length/2+14,t2+1]) {
         cube([brd_width,w,t2],true);
       }
       // Front rail
       color("yellow")
       translate([0,38-brd_length/2-w/2,t2+1]) {  // x,y,z
         cube([brd_width+10,w,t2],true); // Extra width for support
       }
    
    }
    // Screw holes are 71 mm apart, and 72mm front-to back
    union() {
      translate([0,23,0]) {
        screw_hole(-35.5,36); 
        screw_hole(35.5,-36);
        screw_hole(-35.5,-36);
        screw_hole(35.5,36);
      }
    }
  }
}

module screw_hole(x,y) {
    sr = 2.5;          // Radius for screw hole
    sl = 20;           // Length
    translate([x,y,8])
    cylinder(sl,sr,sr,true,$fn=128);
}

// Additional support near servo mount
module support_front(x,y,z) {
    color("green")
     translate([x,y,z])
     rotate([270,36,270]) {
    linear_extrude(height=2,center=true) {
        polygon(points=[[0,0],[0,22],[5,22],[12,0]]);
    }
  }
}

// Back-side handle for wire tie
module tie_handle() {
    r  = 8;    // Handle radius
    t  = 3;    // Handle thickness
    color("green",1.0) 
    rotate([90,90,90])
     translate([27,36,0]) {
         difference() {
            cylinder(t+1,r,r,true);
            cylinder(t+2,r-t,r-t,true);
         }
    }
}
union() {
  difference() {
    union() {
        load_stl();
        tie_handle();
    }
    back_opening();
  }
  rack();
  support_front(20,3,-12);  
  support_front(-20,3,-12);
}

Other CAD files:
cad/skeleton/arms/shoulder_left.STL
cad/skeleton/legs/hip_z_to_hip_y-connector.STL
cad/skeleton/trunk/i101_to_MX28_link.STL
cad/eyes/EyeCasting/Eye.stl
cad/powerbox/top.scad
cad/eyes/EyeCasting/Casting Snap-fit.stl
cad/eyes/EyeCasting/EyeBlank.stl
cad/eyes/EyeCasting/Painting Base.stl
cad/eyes/EyeMechanics/stl/Bottom Left Lid.stl
cad/eyes/EyeMechanics/stl/Bottom Lid Link (x2).stl
cad/eyes/EyeMechanics/stl/Eye Adaptor (x2).stl
cad/eyes/EyeMechanics/stl/Eye Holder.stl
cad/eyes/EyeMechanics/stl/Fork (x2).stl
cad/eyes/EyeMechanics/stl/PlaceHolder Eye (x2).stl
cad/eyes/EyeMechanics/stl/Servo Block.stl
cad/eyes/EyeMechanics/stl/Sub Base.stl
cad/eyes/EyeMechanics/stl/Top Left Lid.stl
cad/eyes/EyeMechanics/stl/Top Lid Link (x2).stl
cad/eyes/EyeMechanics/stl/Top Right Lid.stl
cad/eyes/EyeMechanics/stl/Y-Arm.stl
cad/face/blocked_face.stl
cad/face/cartoon_head.blend
cad/face/eye.blend
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

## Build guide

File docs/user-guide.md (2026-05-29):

# User Guide

This document is a "how-to" user guide describing techniques required to operate specific features of the Bert robot.
Refer to [implementation](http://github.com/chuckcoughlin/bert/tree/master/docs/implementation.md) for detailed descriptions of feature designs and the code behind them.

***************************************************************
## Table of Contents 
  * [Speech](#speech)
    * [Startup](#startup)
    * [Example Statements](#example)
    * [Vocabulary](#vocabulary)
  * [Android Application](#android)

*********************************************************
### Speech 
  The primary method of command and control is via spoken English commands. If a command, statement or question is not recognized, Bert will respond with an appropriate request for clarification. A typical interaction
  may be found [here](https://www.youtube.com/watch?v=ZoP7b5YDawg)
*********************************************************
#### a - Startup 
Once the robot is powered on, a boot sequence commences. On completion, Bert announces a randomized "Ready" statement.
*********************************************************
#### b - Example Statements 
The lists below show typical statements that Bert will recognize.
The full range of understanding comes from combining these patterns with
options from the vocabulary list in the next section.
##### Commands
```
  describe your configuration
  halt
  list the speeds of your motors
  move your left knee to 135 degrees
  move it to 120 degrees
  move the other knee to 120 degrees
  move slowly
  straighten up
```
Commands also include directives to set poses. The command is simply the pose name.
```
   attention
   relax
```
Pose names are not fixed parts of the syntax, but rather names of stored entries in
the robot database.

For additional examples see [testplan](https://github.com/chuckcoughlin/bert/tree/master/docs/testplan.md).

##### Queries
```
    How old are you
    what are the limits on your right elbow (EEPROM hard limits)
    what are the targets for your neck horizontal (position, speed, torque)
    What is your height
    What is the id of your left shoulder vertical
    What is the vertical position of your neck
    what is your left ankle temperature
    why do you wear mittens
```
##### Settings
Infrequently it may be necessary to inform the robot of some fact.
```
  you are "sitting"
  save your pose as "saluting"
  "sit" means to become "sitting"
  when I say "sit" take the pose "sitting"
```
*********************************************************
#### Poses
A *Pose* is a static positioning of the robot.
It is defined by the combined positions of all the joints. The following shows a sequence of steps
that save an arbitrary pose whose positions are created by manual intervention.
A subsequent section will demonstrate combining poses to create an action.

 After startup joints are set to support maximum load and can't be bent by hand.
```
    relax your right arm
```
At this point the torque for the right elbow and associated shoulder joints is disabled.
They can be moved manually to any desired position. Note that the leg "limb" includes hips.
```
  hold it
```
Stiffen the arm, holding it in place so that another limb can be manipulated.
```
  freeze
```
This command freezes all joints as the robot is currently positioned.

  Next, assign a name to the current position
of the robot.   NOTE: In the
samples that follow, names that are substitutable parameters are shown in quotes.
The quotes should not be used when typing commands into the terminal application
as they will not be generated by the speech processor. Likewise the name itself must
be chosen to match the spelling that will be used by the tablet spoken text generator.
```
    your pose is "saluting"
    you are "sitting"
    save that pose
```
Any of these commands record the pose positions in the robot's internal database. If no name
is given a number will be assigned. Note that the pose is now stored on the robot. If the
development machine holds the canonical form of the database, then rows added to the "pose"
table will need to be exported and imported onto the development machine.

A video example of this process may be found [here](https://www.youtube.com/watch?v=3lilrxy11Ac).
*********************************************************
### c - Vocabulary 
"Bert" has a fixed vocabulary when it comes to names of parameters in
various categories.
  * Appendages: ear, eye, finger, nose, toe
  * Axes: x, y, z, horizontal, vertical
  * Body parts (joints): abs, ankle, arm, bust, chest, elbow, head, hip,
  knee, neck, shoulder
  * Commands: exit, freeze, halt, relax, shutdown, stop
  * Core property: age, cadence, cycle time, duty cycle, height, name
  * Joint Properties: id, maximum angle, minimum angle, motor type, offset,
     orientation, position, speed, temperature, torque, voltage
  * Limbs: arm, leg, torso
  * Sides: left, right, other

*********************************************************
  ### Android Application 
  [toc](#table-of-contents)

The Android tablet is a vital part of the robot control system. It provides
voice services (both interpretive (listening) and spoken). The tablet must be
within ~10' for Bluetooth communication. It may be placed conveniently in the
backpack worn by the robot.

The control application is called ***BertSpeak***, and, while it must be running,
there is no necessary interactive control other than speech. The screens shown
below provide some minimal troubleshooting capabilities.

Make sure that the application is configured in the Settings with Permission for Microphone, Camera and Storage.
Additionally, under Settings->General Management, choose the preferred text-speech engine.
(I chose Samsung over Google). Install voice data (I chose a British male).

*********************************************************
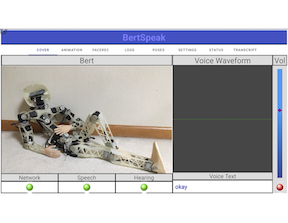
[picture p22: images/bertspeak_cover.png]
BertSpeak
  
 ```                        BertSpeak - Cover Page ```</br>
  The **cover** panel shows the current status of the application, including state of connection with the main robot processor and the most recent text command or response. There are also buttons which turn speech and hearing capabilities on or off. There is also a button to stop the entire application.

  ********************************************************
   ![BertSpeak](/images/bertspeak_animation.png)
 ```                        BertSpeak - Animation Page ```</br>
    The **animation** page shows a stick-figure representataion of the robot in three projections.
    The figures update in real-time to show the current
    robot position. Planned updates will allow the user to drag limbs of the stick-figure and effect actual
    robot positioning.

  ********************************************************
   ![BertSpeak](/images/bertspeak_facerec.png)
 ```                        BertSpeak - Facial Recognition Page ```</br>
    The **facial recognition** page allows a name to be associated with the face of a user. When the user is positioned in front
    of the tablet, the **Analyze** button will either create
    a face entry associated with the name, or will issue a
    presonalized greeting if the facial image is recognized.

  ********************************************************
   ![BertSpeak](/images/bertspeak_logs.png)
 ```                        BertSpeak - Log Page ```</br>
    This page displays log messages that may originate either from the application or the robot.

  ********************************************************
   ![BertSpeak](/images/bertspeak_settings.png)
 ```                        BertSpeak - Settings Page ```</br>
    It is important that the settings be filled in before attempting to use the tablet
    for robot control. The **Settings** page should show the following values:

  ```
    Paired Device         bert_humanoid
    Simulated Connection  false
  ```
   Setting the simulator "true" turns off several features incompatible the Android simulator and is used only during
   development.
  ********************************************************

   ![BertSpeak](/images/bertspeak_transcript.png)
 ```                        BertSpeak - Transcript Page ```</br>
    The **transcript** view records all messages between the robot and applicaion. Outgoing commands are rendered in black, responses from the robot in blue.

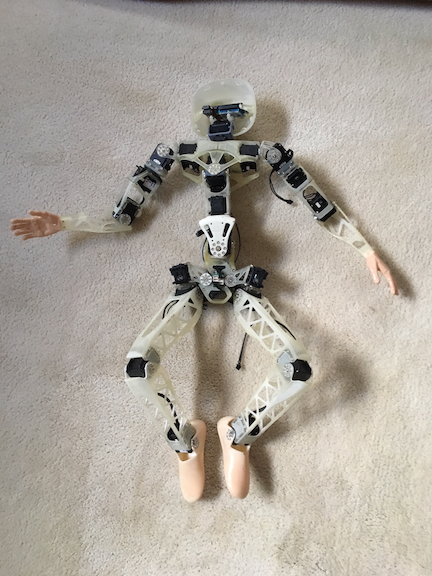
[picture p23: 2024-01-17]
images/skeletal_assembly.png

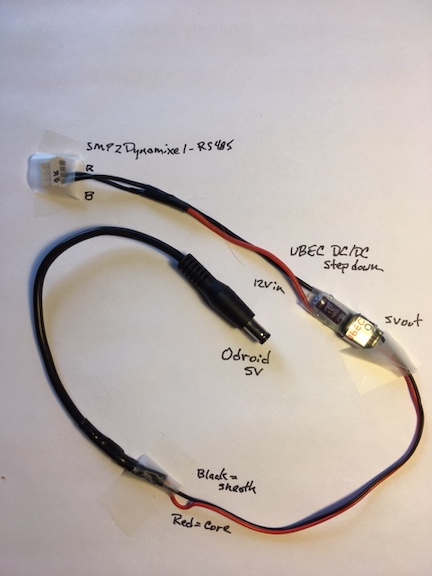
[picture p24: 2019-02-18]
images/5volt_step_down.jpg

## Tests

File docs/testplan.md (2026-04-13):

## Test Plan

This document lays out a series of feature tests for the "Bert" project. Those tests which have passed are marked with green (green). Features that are currently in a broken state and are
actively being debugged are marked in red (red).  A yellow (yellow) marker indicates a feature that has yet to be tested in the current version.
Gray (gray) indicates features that are defined but not yet implemented. The collection of
green markers is a pretty fair indication of completion status of the project.

Unless otherwise stated, tests are run by giving typed commands to the stand-alone version of the robot control code.

***************************************************************
## Table of Contents 
 * [Robot](#robot)
   * [Startup](#startup)
   * [Configuration](#configuration)
   * [Properties](#properties)
   * [Utilities](#utilities)
   * [Movement](#movement)
   * [Actions and Poses](#poses)
   * [Motion Planning](#planning)
   * [Parameters](#parameters)
   * [Miscellaneous](#miscellaneous)
 * [Tablet](#tablet)
   * [Speech](#speech)
   * [BertSpeak](#bertspeak)
 * [Raspberry Pi](#raspberry)
     * [Eye Tracking](#eye)
     * [Blink](#eyelid)

*********************************************************
## Robot 
This section describes tests of the Odroid system, the robot itself.
### a - Startup and Test 

* green ``System Scripts``  - Launch the robot code autonomously on system boot or standalone from the command-line.
- [x] bert-server start/stop: Start/stop the "headless" version of the robot code.
- [x] bert-standalone: Run the robot code from the command line. (Cannot be run simultaneously with daemon).
* green ``Utility Applications``  - Exercise features independent of the robot
application. These are *python3* scripts.
- [x] dxl_scan: Show ids of all connected Dynamixel controllers. Verify that the discovery operation shows the correct motor ids within each serial device (*ttyACM0* and *ttyACM1*).
- [x] dxl_read: Read parameters of a servo motor. Access each individual motor. Verify that parameter settings match values in *bert.xml*.
- [x] dxl_write: Set volatile values for a given motor.
- [x] test-client: Connect via sockets to a running version of the robot. Type commands, receive responses.
interface for interactive testing.
- [x] test-server: Allow the tablet client to connect via sockets to a mock version of the robot. Accept commands, send responses.
interface for interactive testing. Note: when testing with the Android emulator connect the server to *localhost*, but configure
the emulator client as 10.0.2.2.

### b - Configuration 
This section contains tests that validate the wiring and addressing of stepper
motors, the conversion of raw readings from the motors into proper engineering
units, and the listing of various parameters in the motor control tables.  
There are two sets of commands available. The first set is provided for direct
communication from the robot to the tablet, and the second is designed for
spoken user interaction.

* green ``JSON Lists`` - JSON is used internally for direct communication (unspoken) between the tablet and robot.  JSON results are
generated by the command `download`. When displayed the message response is in a JSON pretty-print format.
Available parameters include: position, speed, load, voltage and temperature. For position, either current or goal values are available. Values for static parameters come directly from the XML configuration file, dynamic properties are read from the motors. The tester should verify that results are given in applicable engineering units.

 Additionally user-defined quantities like face names,  poses and actions are available.

Typical requests:
```
    download your static motor parameters
    download the dynamic properties of your joints
    download the names of your joints
    download your limbs
    download your end effectors
    download your joint positions
    download the speeds of your motors
    download your motor ids
    download your poses
    download your face names
```
* green ``Name Lists`` -
Each of the parameter sets listed above can be displayed
in a space-separated list simply by using the verb
`list` or one of several synonyms.  The space-separated list which makes them pronounceable by the tablet.
Using the verb `download` results in the same information, but expressed in JSON.
This matches the message format for communication with the tablet.
Typical requests:
```
    download your joints
    list your motor ids
    list your joint positions
    tell me the llimits of your left elbow y
    tell me your static motor parameters
    list the angles of your joints
    list the torque of your motors
    list the speeds of your motors
    what are the dynamic properties of your joints
    what are the names of your joints
    what are the names of your limbs
    what are the names of your appendages
    what are the names of your poses
    what poses do you know
    who do you know
```

* yellow ``Goals`` - Goals refer to target positions
of commanded movements. Limits refer to the maxima and minima of motor parameters.
These are configured in motor EEPROM settings and cannot be changed.  
While in-transit, the current position will not match the goal. Test at very slow velocities. Goal and limit parameters
include angle, speed and and torque limits.  Speeds are degrees/sec and
torques are newton-meters. Results are given in JSON format.
Typical syntax:
```
    what are the target positions of your left shoulder x
    list the limits of your right ankle
```

### c - Properties 
The following commands are meant for direct feedback to the user.
They deal with individual joints.

* green ``Joint Properties`` - Use the terminal application, *bert-standalone*, to
read the current values of joint properties, one by one. A complete list of joint names and properties may be found
in the *Vocabulary* section of the user guide. In addition to properties configured in the configuration
file (like: id, motor type, orientation, minimum angle and maximum angle), properties include current
values read directly from the motor (like: position (degrees), speed (degrees/sec), load (N-m), torque (N-m),
temperature (deg C), and voltage (volts). A typical query:
```
    what is the id of your left hip y
    what is the position of your left elbow
    what is your right ankle position
    what is the speed of your right knee
    what is the temperature of your right shoulder x
    what is the torque of your left hip x
    what is the range of your right knee
    what is the maximum angle of your left elbow
    what is the maximum speed of your right ankle
    what is the maximum torque of your left shoulder y
```
* green ``Range of Motion`` - Test limits
that are configured in each motor's EEPROM. (Units must be flashed individually to change these.)
Additionally these values are configured in  *bert.xml*. Test to make sure that each joint
can be driven to the minimum and maximum of its range - and that these range values make sense
for the movement of the robot as a whole. Caution some of these settings may conflict with each other. There is no collision checking.
- [x] abs (x,y,z)      range: (150,210),(150,200),(-60,60)
- [x] ankle            range: (60,135)
- [x] chest (x,y)       range: (170,190),(170,190)
- [x] elbow            range: (45,180)
- [x] knee             range: (50,180)
- [x] hip (x,y,z)      range: (155,190),(75,225),(-20,45)
- [x] neck (y,z)        ranges: (-5,20),(30,30)
- [x] shoulder (x,y,z)  ranges: (90,215),(0,225),(-45,90)

### d - Utilities 

* green ``Initialization`` - set the position of each joint to its default. Use the standalone version of the robot application to enter the command then visually verify the position of each joint. Note that after startup each joint is
guaranteed to be in a sane position. This command relies on a built-in pose.
```
    straighten up
```
* gray ``System Commands`` - These are no-argument commands that
perform various system operations. In the list below, the check mark indicates completion.
  - [x] halt: stop the control processes on the robot. Leave the operating system running.
  - [ ] reset: clear any unprocessed results from the serial ports. This is an internal recovery
  operation in the event of I/O errors.
  - [ ] shutdown: power off the robot after a clean shutdown.

* green ``Sane Startup`` - When the robot is first powered on,
its limbs are in unknown positions. As part of the startup sequence, read the positions of
all joints and move those that are outside configured limits to the closest "legal" value.
When this initialization is complete, a response is issued stating that the robot is ready.

This command may be issued at any time. It is most often needed after a *relax*
```
  initialize joints
```

### e - Movement 
[toc](#table-of-contents)<br/>
This section describes the first set of tests for driving the position of the robot.
It also introduces use of the database to store "poses". The tests here simply
drive joints to a goal. There is not yet a concept of trajectory planning.

* green ``Move Joint`` - Using the terminal application,
move a joint to a specified position. Make sure that any attempts to drive it
out-of-range are clipped . Sample command syntax:
```
    move your left knee to 90 degree
    turn your right thigh x to 180
    set the left elbow position to 90 degrees
    set the position of your left ankle to 60
    set the left elbow to 90
    straighten your left knee
```
* green ``Pronouns`` - Show the use of 'it' as a substitution for
the last referenced joint or side. Show the use of 'other' as a substitution for the joint on the opposite side of the previously referenced joint. Sample command syntax:
```
    move it to 20
    set your other elbow to 90
    straighten it
```
* green ``Change speed or torque`` - Using the terminal application,
change the speed or torque of a joint. Both speed and torque are expressed in engineering units
(degrees/second and newton-meters, respectively).
Sample command syntax:
```
    set the speed of your right elbow to 200
    set the torque of your other elbow to 1.2
    set the speed of your left leg to slow
    move normally
    move quickly
    move very slowly
    move slower
    go faster
```
The "move" and "go" commands set speeds for future movements of all joints at once.

* green ``Enable torque`` - Dynamixel motors may be
configured to be freewheeling and compliant or stiff. The term for this feature
is "torque enable". Our names are "relax" and "freeze". These commands may be applied to individual joints, limbs or the entire robot.
Sample command syntax:
```
    relax your right arm
    freeze your right elbow
    hold it
    relax
    freeze
    go rigid
    go limp
    straighten up
```
Note that the Dynamixel motors automatically enable torque whenever a position is set (otherwise there
would be no point). Additionally, whenever a joint is stiffened, the position is read and recorded as "current".

### f - Actions and Poses 
A ``pose`` is a collection of joint positions which can be summoned by name. An ``action`` is a collection
of poses executed in order with sufficient time delays to allow movement to each pose to complete. For
clarity each pose within the same action can be given the same name plus an index that defines execution
order. JSON versions of the commands are supplied to facilitate editing on the tablet.

* green ``Pose`` - Associate the current joint positions with
a named pose. The pose is saved in the robot's internal database and represents a collection of joint-position pairs. The pose is given an index (1 by default) to allow poses of the same name to all be part of an action.

In the examples that follow *saluting* is a pose name and *salute* is an action.
```
    your pose is saluting
    this is saluting 1
    you are saluting 1
    save your pose as saluting 3
    record it as saluting 2
```
In the case where an index is not specified,
the robot will use the most recently referenced index.

Some requests are designed for direct tablet interaction and return a JSON string
```
    describe the current pose
    describe pose saluting 2
```

* green ``Actions`` - Associate an action (command)
with a series of pre-defined poses.  Pose and action names are
arbitrary, but must be spelled in the same
way as the Android text-to-speech processor. Sample syntax:
```
  define salute as a series of saluting poses
  when I say salute use saluting
```
Actions may be chained by defining a second action to be executed after the first.
Defining an action to be executed after itself results in a loop that has to be
explicitly cleared. All followon definitions are cleared on startup of the control application.
```
    follow salute with wave
    follow wave with wave
    stop waving
```
As before some requests are designed for direct tablet interaction and return a JSON string
```
    describe action salute
```

* green ``Command`` - Either the name of an action or single pose
may be used to drive the robot to a previously stored
pose or execute some action.  As of yet, this movement does not account for positional conflicts.
```
    salute
    saluting 2
    assume the pose saluting
    take the pose saluting 3
```

* green ``Clean up`` - Remove a face,
 pose or action. If an action is
deleted, all of the poses referencing that action are also deleted. If no pose index is given
all poses of the specified name are deleted.
```
    forget action salute
    forget pose saluting 1
    delete face charlie
```

### g - Motion Planning 
[toc](#table-of-contents)<br/>
Plan motions so as to bring end effectors to a certain position and avoid collisions
between different parts of the robot. A prerequisite to planning
involves calculation of the 3 dimensional location of each limb.

* yellow ``Forward Kinematics`` - Query the robot to determine its understanding
of the location of its joints or end effectors. The result consists of distances (~mm) in three dimensions
of the target to the origin which is the center of the pelvis.
```
    where is your left hand
    where are your eyes
    where is your right ear
```
The object of the question may be either an "end effector" (as used in the examples) or a joint.
An end effector is simply a protuberance somewhere on a limb. In our setting, it has no controllable parts.
The 'URDF' file defines legal names.
In addition to validating that the syntax works, check numeric results for the following:
  - [x] ABS_Y: this is the first joint, at the top of the Pelvis. Its position should never change.
  - [x] ABS_X: connected on top of ABS_Y, verify its position as ABS_Y is moved.
  - [x] ... and so on. Follow the joints in order until reaching the left finger (an end effector).
  - [x] ... likewise, follow the joints in order until reaching the right finger.
  - [x] RIGHT_HIP_X: this is the first joint in a sub-chain. Its position should never change.
  - [x] ... as before, follow this chain of joints to the right toe.
  - [x] ... likewise, follow the left hip sub-chain to the left toe.
  - [x] NOSE: make sure that the HEAD calculations are correct.

### h - Static Parameters 
[toc](#table-of-contents)<br/>
Test the ability to query performance metrics from the dispatcher. These do not involve
the stepper motors
* green ``Metrics`` - use the terminal application to query
the dispatcher for: name, age, height, cadence, cycle time, duty cycle and cycles processed.
The results should be formatted into proper english sentences. Typical syntax:
```
  what is your name
  how tall are you
  what is your age
  what is the cycle count
```

### i - Miscellaneous 
This section includes tests of irregular or one-off speech patterns.
* green ``Misc``  - these are statements outside the regular
syntax shown above that are processed in a reasonable manner.
```
    hi bert
    move in slow motion
    why do you wear mittens
```

* green ``Unrecognized commands`` -
Whenever the robot is unable to decipher the syntax of a command, the text is simply forwarded to Chat GPT for an answer. Of course, the interchange will have no effect on robot actions.
Sample requests:
```
    why is the sky blue
    what do think of Chuck
```

* yellow ``Desired``  - the list below consists of statements or queries
that are useful, but not currently recognized.<br/>

## Tablet 
Describe tests specifically for the Android tablet application called "BertSpeak"

[toc](#table-of-contents)<br/>
### a - Tablet Application 

The <b>Cover</b> page of the `BertSpeak` application shows a reclining picture of the robot and an audio visualizer. It also contains status buttons which show the
status of the connection to the robot, the states of speech
to text and of text to speech processing. The right-side slider adjusts the speaking volume.
The red button in the lower right corner kills the tablet application.

Cover

* yellow ```Ignoring``` -
It can be annoying when the robot
attempts to interpret  background speech not directed  towards it.
(And usually fails).
The commands below place the tablet application into a state where it ignores ambient speech until specifically directed to be attentive. Note: The `cover` tab has a "Hearing" button that performs the same function.
  ```
      Bert, ignore me
      Bert, pay attention
  ```

The <b>Facial Recognition</b> page shows a view from the
forward-facing camera. A button press allows the user to
analyze the image for a human face.

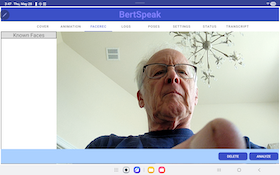
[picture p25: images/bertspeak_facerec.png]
Facial Recognition


* green ```Detecting``` - if a
face is detected, but is not known from a previous analysis,
the robot will query for a name and expect a response.
```
    What is your name
    my name is Chuck
```
* green ```Greeting``` - if a
face is detected and matches a face previously analyzed,
the robot will send a greeting.
```
    Hi Chuck
```

This is the facial recognition page that
allows the robot to recognize whoever is handling the tablet.

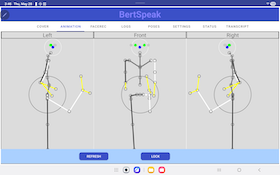
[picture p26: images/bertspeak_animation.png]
Animation


* yellow ```Animation```

This panel is planned to show the robot position
in real-time .

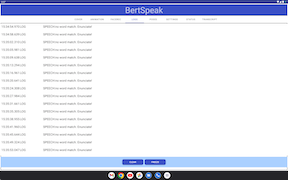
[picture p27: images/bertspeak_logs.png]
Logging


* yellow ```Logging```

Validate that notifications and internal
application errors are logged to this panel.

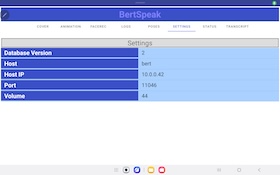
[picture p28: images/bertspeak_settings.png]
Settings


* green ```Settings```

There are a small number of configurable parameters
that are settable on this page.

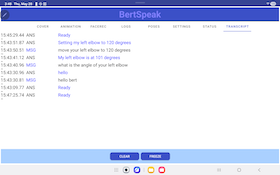
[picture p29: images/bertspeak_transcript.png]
Transcript

* yellow ```Transcript```

Validate that the tablet keeps a record of spoken commands and corresponding responses from the robot.

### b Speech 

Test the integration of the android tablet with the robot as it involves
spoken text.
* green ``Speech`` - Validate that all commands and queries
used in the previous section can be executed via speech and that responses are
likewise formulated into audible sentences.

## Raspberry Pi
This section describes test on the Raspberry Pi auxiliary system, the sub-processor that handles
smaller appendages.
### a - Eye Tracking 
### b - Blink

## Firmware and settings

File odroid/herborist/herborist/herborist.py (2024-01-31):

import sys
import time
import itertools
import threading

from PyQt5.Qt import QApplication, QTreeWidgetItem, QMessageBox
import PyQt5.QtCore as QtCore
import PyQt5.uic as uic

from collections import defaultdict
from pkg_resources import resource_filename

import pypot.dynamixel


# MARK: - DxlIO connection

__dxl_io = None
__lock = threading.Lock()


def get_dxl_connection(port, baudrate, protocol="MX"):
    global __dxl_io

    __lock.acquire()
    if protocol == "XL":
        __dxl_io = pypot.dynamixel.Dxl320IO(port, baudrate, use_sync_read=False)
    else:
        __dxl_io = pypot.dynamixel.DxlIO(port, baudrate, use_sync_read=False)
    return __dxl_io


def release_dxl_connection():
    __dxl_io.close()
    __lock.release()


class HerboristApp(QApplication):
    def __init__(self, argv):
        QApplication.__init__(self, argv)
        self.window = uic.loadUi(resource_filename('herborist','herborist.ui'))

        self.enable_motor_view(False)

        # slider / lcd connections
        self.window.rdt_slider.valueChanged.connect(self.window.rdt_lcd.display)
        self.window.torque_max_slider.valueChanged.connect(self.window.torque_max_lcd.display)
        self.window.lower_limit_dial.valueChanged.connect(self.window.lower_limit_lcd.display)
        self.window.upper_limit_dial.valueChanged.connect(self.window.upper_limit_lcd.display)
        self.window.present_position_dial.valueChanged.connect(self.window.present_position_lcd.display)
        self.window.goal_position_dial.valueChanged.connect(self.window.goal_position_lcd.display)

        # Connect the button to their cb
        self.window.scan_button.pressed.connect(self.start_scanning)
        self.window.abort_button.pressed.connect(self.abort_scanning)

        # We manually uncheck most baudrates in the selection list
        # as unchecking them in the ui editor make the checkbox goes away
        for i in range(1, len(self.window.baudrate_list)):
            self.window.baudrate_list.item(i).setCheckState(False)

        # We prevent the minimum id to be greater than the maximum id
        def min_id_changed(self, new_id):
            if new_id >= self.window.max_id.value():
                self.window.min_id.setValue(self.window.max_id.value())

        def max_id_changed(self, new_id):
            if new_id <= self.window.min_id.value():
                self.window.max_id.setValue(self.window.min_id.value())

        self.window.min_id.valueChanged.connect(lambda i: min_id_changed(self, i))
        self.window.max_id.valueChanged.connect(lambda i: max_id_changed(self, i))

        # We automatically refresh the port list
        self.refresh_port_thread = self.UpdatePortThread()
        self.refresh_port_thread.port_updated.connect(self.update_port)
        self.refresh_port_thread.start()

        # Motor View
        self.window.motor_tree.itemSelectionChanged.connect(self.update_motor_view)
        self.window.goal_position_dial.valueChanged.connect(self.update_motor_position)
        self.window.update_eeprom_button.pressed.connect(self.update_eeprom)
        self.window.torque_checkbox.stateChanged.connect(self.switch_torque)

        self.refresh_motor_thread = None

    # MARK: - Port update

    class UpdatePortThread(QtCore.QThread):
        port_updated = QtCore.pyqtSignal(list)

        def __init__(self):
            QtCore.QThread.__init__(self)
            self.daemon = True

        def run(self):
            while True:
                new_ports = pypot.dynamixel.get_available_ports()
                self.port_updated.emit(new_ports)
                time.sleep(0.1)

    def update_port(self, new_ports):
        old_ports = []
        for i in range(len(self.window.port_box)):
            old_ports.append(str(self.window.port_box.itemText(i)))

        selected_port = self.window.port_box.currentText()

        if old_ports != new_ports:
            self.window.port_box.clear()
            self.window.port_box.addItems(new_ports)

            for i in range(len(self.window.port_box)):
                if self.window.port_box.itemText(i) == selected_port:
                    self.window.port_box.setCurrentIndex(i)
                    break

            if old_ports and not new_ports:
                self.window.scan_button.setEnabled(False)
            elif not old_ports and new_ports:
                self.window.scan_button.setEnabled(True)

    # MARK: - Motor Scan
    def update_motor_tree(self, baud_for_ids):
        self.window.motor_tree.clear()

        for b, ids in baud_for_ids.items():
            baud_root = QTreeWidgetItem(self.window.motor_tree, [str(b)])
            baud_root.setExpanded(True)
            f = int(baud_root.flags()) - int(QtCore.Qt.ItemIsSelectable)
            baud_root.setFlags(QtCore.Qt.ItemFlags(f))

            dxl_io = get_dxl_connection(self.port, b, self.protocol)
            models = dxl_io.get_model(ids)
            release_dxl_connection()

            for id, model in zip(ids, models):
                QTreeWidgetItem(baud_root, ['', str(id), model])

    def start_scanning(self):
        self.window.scan_button.setEnabled(False)
        self.window.motor_tree.setEnabled(False)
        self.window.abort_button.setEnabled(True)

        self.window.motor_tree.clear()

        baudrates = []
        for i in range(len(self.window.baudrate_list)):
            checkbox = self.window.baudrate_list.item(i)
            if checkbox.checkState() == 2:
                b = int(checkbox.text())
                if b == 57600 and self.usb_device == "USB2DYNAMIXEL":
                    b = 57142
                baudrates.append(b)

        id_range = list(range(self.window.min_id.value(), self.window.max_id.value() + 1))

        self.window.scan_progress.setValue(0)
        self.window.scan_progress.setMaximum(len(baudrates) * len(id_range) - 1)

        self.scan_thread = self.ScanThread(self.port, baudrates, self.protocol, id_range,
                                           self.window.motor_tree, self.window.scan_progress)
        self.scan_thread.done.connect(self.done_scanning)
        self.scan_thread.part_done.connect(self.window.scan_progress.setValue)
        self.scan_thread.start()

    def abort_scanning(self):
        self.scan_thread.abort()

    def done_scanning(self):
        self.window.motor_tree.setEnabled(True)
        self.window.abort_button.setEnabled(False)
        self.window.scan_button.setEnabled(True)

    class ScanThread(QtCore.QThread):
        done = QtCore.pyqtSignal()
        part_done = QtCore.pyqtSignal(int)

        def __init__(self, port, baudrates, protocol, id_range,
                     motor_tree, scan_progress):

            QtCore.QThread.__init__(self)
            self.daemon = True

            self.running = threading.Event()
            self.running.set()

            self.port = port
            self.baudrates = baudrates
            self.protocol = protocol
            self.id_range = id_range

            self.motor_tree = motor_tree
            self.scan_progress = scan_progress

        def run(self):
            for b in self.baudrates:
                baud_root = QTreeWidgetItem(self.motor_tree, [str(b)])
                baud_root.setExpanded(True)
                f = int(baud_root.flags()) - int(QtCore.Qt.ItemIsSelectable)
                baud_root.setFlags(QtCore.Qt.ItemFlags(f))

                dxl_io = get_dxl_connection(self.port, b, self.protocol)

                for id in self.id_range:
                    if not self.running.is_set():
                        break

                    if dxl_io.ping(id):
                        model = dxl_io.get_model((id, ))[0]
                        QTreeWidgetItem(baud_root, ['', str(id), model])

                    self.part_done.emit(self.scan_progress.value() + 1)

                release_dxl_connection()

            self.done.emit()

        def abort(self):
            self.scan_progress.setValue(0)
            self.running.clear()

    # MARK: - Motor View
    def update_motor_view(self):
        if self.refresh_motor_thread:
            self.refresh_motor_thread.stop()
            self.refresh_motor_thread.wait()

        if not self.selected_motors:
            self.enable_motor_view(False)
            return

        self.enable_motor_view(True)

        if len(list(itertools.chain(*list(self.selected_motors.values())))) > 1:
            for widget_name in ('id_spinbox',
                                'present_position_dial',
                                'goal_position_dial',
                                'present_position_lcd',
                                'goal_position_lcd'):
                getattr(self.window, widget_name).setEnabled(False)

        dxl_io = get_dxl_connection(self.port, self.baudrate, self.protocol)
        srl = dxl_io.get_status_return_level((self.id, ), convert=False)[0]
        if srl != 0:
            model = dxl_io.get_model((self.id, ))[0]
            rdt = dxl_io.get_return_delay_time((self.id, ))[0]
            firmware = dxl_io.get_firmware((self.id, ))[0]
            torque_max = dxl_io.get_max_torque((self.id, ))[0]
            angle_limit = dxl_io.get_angle_limit((self.id, ))[0]
            goal_pos = dxl_io.get_goal_position((self.id, ))[0]
            torque_enable = dxl_io.is_torque_enabled((self.id, ))[0]
        release_dxl_connection()

        self.window.id_spinbox.setValue(self.id)

        for i in range(len(self.window.baud_combobox)):
            if int(self.window.baud_combobox.itemText(i)) == self.baudrate:
                self.window.baud_combobox.setCurrentIndex(i)
                break

        self.window.srl_combobox.setCurrentIndex(srl)

        if srl != 0:
            self.window.rdt_slider.setValue(rdt)
            self.window.firmware_label.setText(str(firmware))
            self.window.torque_max_slider.setValue(torque_max)

            limit = 180 if model.startswith('MX') else 150
            for widget_name in ('lower_limit_dial', 'upper_limit_dial',
                                'present_position_dial', 'goal_position_dial'):
                getattr(self.window, widget_name).setMinimum(-limit)
                getattr(self.window, widget_name).setMaximum(limit)

            self.window.lower_limit_dial.setValue(angle_limit[0])
            self.window.upper_limit_dial.setValue(angle_limit[1])
            self.window.goal_position_dial.setValue(goal_pos)
            self.window.torque_checkbox.setChecked(torque_enable)

        self.refresh_motor_thread = self.UpdateMotorThread(self.port, self.baudrate, self.protocol, self.id)
        self.refresh_motor_thread.position_updated.connect(self.motor_position_updated)
        self.refresh_motor_thread.start()

    def update_motor_position(self, pos):
        if self.window.torque_checkbox.checkState():
            dxl_io = get_dxl_connection(self.port, self.baudrate, self.protocol)
            dxl_io.set_goal_position({self.id: pos})
            time.sleep(0.05)
            release_dxl_connection()

    def motor_position_updated(self, pos):
        self.window.present_position_dial.setValue(pos)

    def switch_torque(self, torque_enable):
        if torque_enable:
            self.window.goal_position_dial.setEnabled(True)
            self.window.goal_position_lcd.setEnabled(True)
        else:
            self.window.goal_position_dial.setEnabled(False)
            self.window.goal_position_lcd.setEnabled(False)

        for b, ids in self.selected_motors.items():
            dxl_io = get_dxl_connection(self.port, b, self.protocol)
            (dxl_io.enable_torque if torque_enable else dxl_io.disable_torque)(ids)
            time.sleep(0.05)
            release_dxl_connection()

    def enable_motor_view(self, enabled):
        for i in range(len(self.window.motor_layout)):
            self.window.motor_layout.itemAt(i).widget().setEnabled(enabled)

    def update_eeprom(self):
        if self.refresh_motor_thread:
            self.refresh_motor_thread.stop()
            self.refresh_motor_thread.wait()

        rdt = self.window.rdt_slider.value()
        srl = self.window.srl_combobox.currentIndex()
        torque_max = self.window.torque_max_slider.value()
        lower_limit = self.window.lower_limit_dial.value()
        upper_limit = self.window.upper_limit_dial.value()
        new_id = self.window.id_spinbox.value()

        for b, ids in self.selected_motors.items():
            dxl_io = get_dxl_connection(self.port, b, self.protocol)
            dxl_io.set_return_delay_time(dict(list(zip(ids, itertools.repeat(rdt)))))
            dxl_io.set_status_return_level(dict(list(zip(ids, itertools.repeat(srl)))), convert=False)
            dxl_io.set_max_torque(dict(list(zip(ids, itertools.repeat(torque_max)))))
            dxl_io.set_angle_limit(dict(list(zip(ids, itertools.repeat((lower_limit, upper_limit))))))
            time.sleep(0.15)
            release_dxl_connection()

        new_ids = self.ids.copy()

        old_ids = list(self.selected_motors.values())
        if len(old_ids) == 1 and len(old_ids[0]) == 1 and new_id != old_ids[0][0]:
            b, old_id = list(self.selected_motors.keys())[0], old_ids[0][0]
            dxl_io = get_dxl_connection(self.port, b, self.protocol)
            try:
                dxl_io.change_id({old_id: new_id})

                l = new_ids[b]
                l[l.index(old_id)] = new_id
                new_ids[b] = l

            except ValueError:
                QMessageBox.about(self.window,
                                              '',
                                              'This id is already used.')
                pass

            release_dxl_connection()

        for b, ids in self.selected_motors.items():
            new_b = int(self.window.baud_combobox.currentText())
            if b != new_b:
                dxl_io = get_dxl_connection(self.port, b, self.protocol)
                dxl_io.change_baudrate(dict(list(zip(ids, itertools.repeat(new_b)))))
                time.sleep(0.1)
                release_dxl_connection()

            for id in ids:
                new_ids[new_b].append(id)
                new_ids[b].remove(id)
                new_ids[new_b].sort()

        self.update_motor_tree(new_ids)

    class UpdateMotorThread(QtCore.QThread):
        position_updated = QtCore.pyqtSignal(int)

        def __init__(self, port, baudrate, protocol, mid):
            QtCore.QThread.__init__(self)
            self.running = threading.Event()
            self.running.set()

            self.port = port
            self.baudrate = baudrate
            self.protocol = protocol
            self.mid = mid

        def stop(self):
            self.running.clear()

        def run(self):
            while self.running.is_set():
                dxl_io = get_dxl_connection(self.port, self.baudrate, self.protocol)
                pos = dxl_io.get_present_position((self.mid, ))[0]
                release_dxl_connection()

                self.position_updated.emit(pos)

                time.sleep(0.05)

    # MARK: - Shortcut properties
    @property
    def port(self):
        return str(self.window.port_box.currentText())

    @property
    def protocol(self):
        return str(self.window.protocol_box.currentText())

    @property
    def usb_device(self):
        return str(self.window.usb_device_box.currentText())

    @property
    def baudrate(self):
        return list(self.selected_motors.keys())[0]

    @property
    def id(self):
        return self.selected_motors[self.baudrate][0]

    @property
    def selected_motors(self):
        motors = defaultdict(list)

        selected_items = self.window.motor_tree.selectedItems()
        selected_items = [item for item in selected_items if item.parent()]

        for item in selected_items:
            motors[int(item.parent().text(0))].append(int(item.text(1)))

        return motors

    @property
    def ids(self):
        ids = defaultdict(list)

        root = self.window.motor_tree.invisibleRootItem()
        for i in range(root.childCount()):
            baud_node = root.child(i)

            if baud_node.text(0):
                b = int(baud_node.text(0))
                ids[b]
            else:
                ids[0].append(int(baud_node.text(1)))

            for j in range(baud_node.childCount()):
                id_node = baud_node.child(j)
                ids[b].append(int(id_node.text(1)))

        return ids


def main():
    app = HerboristApp(sys.argv)
    app.window.show()
    sys.exit(app.exec_())

    __lock.acquire()


if __name__ == '__main__':
    main()

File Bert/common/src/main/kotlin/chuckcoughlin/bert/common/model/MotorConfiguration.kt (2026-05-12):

/**
 * Copyright 2022-2025. Charles Coughlin. All Rights Reserved.
 * MIT License.
 */
package chuckcoughlin.bert.common.model

import java.io.Serializable
import java.util.logging.Logger

/**
 * A motor refers to a Dynamixel stepper motor at one of the joints
 * of the robot. Each motor is in a group belonging to a single controller.
 * Optionally it may be part of a "Limb", a group of related motors.
 * All motors in a limb are managed by the same controller.
 *
 * The parameters here are configured in EEPROM. Some may be modifiable
 * at runtime, others are read-only
 * @param j name of the motor (its joint)
 * @param motorType Dynamixel model
 * @param motorId address
 * @param cname controller name
 * @param direct true if orientation is "forward"
 */
class MotorConfiguration(j: Joint, motorType: DynamixelType, motorId: Int, cname: String, direct: Boolean): Serializable {
    val controller: String
    val joint: Joint
    val type : DynamixelType
    val id: Int

    // Setting torque enable is essentially powering the motor on/off
    var isTorqueEnabled : Boolean// Torque-enable - on/off
    var isTorquePending : Boolean// Torque-enable/disable is requested
    var limb: Limb
    var load: Double
    // When we move the joint, set a target position.
    // Update the angle only when movement command has been written.
    // All angles are in degrees.
    var angle : Double
    var goalAngle : Double
    var minAngle : Double
    var maxAngle : Double
    var maxSpeed : Double
    var maxTorque : Double
    var offset : Double // Configured position correction
    var isDirect: Boolean

    var goalSpeed: Double
    var speed = ConfigurationConstants.TOP_SPEED      // ~ degrees/second
        get() = field
        set(value) {
            if(value>0.0) field = value
        }

    var temperature : Double // deg C
    var goalTorque : Double
    var torque : Double // ~ N-m
    var voltage: Double

    /**
     * Set a motor target property given a property enumeration and a value.
     * Attempts to set a read-only value fail silently.
     */
    fun setDynamicPropertyGoal(jp: JointDynamicProperty, value: Double) {
        when (jp) {
            JointDynamicProperty.ANGLE -> goalAngle = value
            JointDynamicProperty.LOAD -> load = value
            JointDynamicProperty.MAXIMUMANGLE -> {}
            JointDynamicProperty.MINIMUMANGLE -> {}
            JointDynamicProperty.SPEED -> goalSpeed = value
            JointDynamicProperty.MAXIMUMSPEED -> {}
            JointDynamicProperty.STATE -> setState(value)
            JointDynamicProperty.TEMPERATURE -> temperature = value
            JointDynamicProperty.TORQUE -> goalTorque = value
            JointDynamicProperty.MAXIMUMTORQUE -> {}
            JointDynamicProperty.VOLTAGE -> voltage = value
            JointDynamicProperty.RANGE -> {}  // Error - max and min must be set separately
            JointDynamicProperty.NONE-> {}
        }
    }
    /**
     * Set a motor actual property given a property enumeration and a value.
     * Attempts to set a read-only value fail silently.
     */
    fun setDynamicProperty(jp: JointDynamicProperty, value: Double) {
        when (jp) {
            JointDynamicProperty.ANGLE -> angle = value
            JointDynamicProperty.LOAD -> load = value
            JointDynamicProperty.MAXIMUMANGLE -> {}
            JointDynamicProperty.MINIMUMANGLE -> {}
            JointDynamicProperty.SPEED -> speed = value
            JointDynamicProperty.MAXIMUMSPEED -> {}
            JointDynamicProperty.STATE -> setState(value)
            JointDynamicProperty.TEMPERATURE -> temperature = value
            JointDynamicProperty.TORQUE -> torque = value
            JointDynamicProperty.MAXIMUMTORQUE -> {}
            JointDynamicProperty.VOLTAGE -> voltage = value
            JointDynamicProperty.RANGE -> {}  // Error - max and min must be set separately
            JointDynamicProperty.NONE-> {}
        }
    }

    private fun setState(s: Double) {
        val state = s.toInt()
        isTorquePending = state != 0
    }

    private val CLSS = "MotorConfiguration"
    private val LOGGER = Logger.getLogger(CLSS)

    /**
     * Set initial values for both definition and runtime parameters.
     */
    init {
        // Read-only
        controller = cname
        id = motorId
        isDirect = direct
        joint = j
        type = motorType
        limb = Limb.NONE
        load = 0.0
        offset = 0.0
        angle = 0.0
        goalAngle = 0.0
        minAngle = -180.0
        maxAngle = 180.0
        maxSpeed = 600.0
        goalSpeed = ConfigurationConstants.TOP_SPEED
        maxTorque = 1.9
        // These are current goal settings
        temperature = 20.0 // Room temperature
        goalTorque = 0.0
        torque = 0.0       // Power-off value
        isTorqueEnabled = true // Initially torque is enabled
        isTorquePending = true
        voltage = 0.0
    }
}

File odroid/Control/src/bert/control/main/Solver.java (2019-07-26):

/**
 * Copyright 2019. Charles Coughlin. All Rights Reserved.
 *                 MIT License.
 */
package bert.control.main;

import java.nio.file.Path;
import java.nio.file.Paths;
import java.util.Collection;
import java.util.List;
import java.util.Map;
import java.util.logging.Logger;

import bert.control.model.Link;
import bert.control.model.TestRobotModel;
import bert.control.model.URDFModel;
import bert.share.common.PathConstants;
import bert.share.control.Appendage;
import bert.share.logging.LoggerUtility;
import bert.share.motor.Joint;
import bert.share.motor.MotorConfiguration;

/**
 *  This class handles various computations pertaining to the robot,
 *  including: trajectory planning. Note that the same link object
 *  may belong to several chains.
 */
public class Solver {
	private final static String CLSS = "Solver";
	private static Logger LOGGER = Logger.getLogger(CLSS);
	private final static double[] ERROR_POSITION = {0.,0.,0.};
	private final URDFModel model;
	private Map<Joint,MotorConfiguration> motorConfigurations;

	/**
	 * Constructor:
	 */
	public Solver() {
		this.model = new URDFModel();
		this.motorConfigurations = null;
	}
	/**
	 * @return the tree of links which describes the robot.
	 */
	public URDFModel getModel() { return this.model; }
	/**
	 * Traverse the tree, setting the current angles from the
	 * motor configurations. Mark the links as "dirty".
	 */
	public void setTreeState() {
		Collection<Link> links = model.getChain().getLinks();
		for(Link link:links) {
			link.setDirty();
			Joint joint = link.getLinkPoint().getJoint();
			MotorConfiguration mc = motorConfigurations.get(joint);
			link.setJointAngle(mc.getPosition());
		}
	}
	/**
	 * Analyze the URDF file for robot geometry. This must be called before
	 * we set a tree state.
	 * @param mc a map of MotorConfigurations
	 * @param urdfPath
	 */
	public void configure(Map<Joint,MotorConfiguration> mc,Path urdfPath) {
		this.motorConfigurations = mc;
		LOGGER.info(String.format("%s.configure: URDF file(%s)",CLSS,urdfPath.toAbsolutePath().toString()));
		model.analyzePath(urdfPath);
	}
	
	/**
	 * Return the position of a specified appendage in x,y,z coordinates in meters from the
	 * robot origin in the pelvis.
	 */
	public double[] getPosition(Appendage appendage) {
		List<Link> subchain = model.getChain().partialChainToAppendage(appendage);
		if( subchain.size()>0 ) return subchain.get(0).getCoordinates();
		else return ERROR_POSITION;
	}
	/**
	 * Return the position of a specified joint in x,y,z coordinates in meters from the
	 * robot origin in the pelvis in the inertial reference frame.
	 */
	public double[] getPosition(Joint joint) {
		List<Link> subchain = model.getChain().partialChainToJoint(joint);
		if( subchain.size()>0 ) return subchain.get(0).getCoordinates();
		else return ERROR_POSITION;
	}
	
	/**
	 * Set the position of a joint. This is primarily for testing. It does not 
	 * cause a serial write to the motor.
	 * @param joint
	 * @param pos
	 */
	public void setJointPosition(Joint joint,double pos) {
		MotorConfiguration mc = motorConfigurations.get(joint);
		mc.setPosition(pos);
	}
	
	/**
	 * Test forward kinematic calculations of various positions of the robot skeleton. 
	 * We rely on configuration file in $BERT_HOME/etc on the development machine.
	 */
	public static void main(String [] args) {
		// Analyze command-line argument to obtain the robot root directory.
		String arg = args[0];
		Path path = Paths.get(arg);
		PathConstants.setHome(path);
		// Setup logging to use only a file appender to our logging directory
		String LOG_ROOT = CLSS.toLowerCase();
		LoggerUtility.getInstance().configureTestLogger(LOG_ROOT);
		// Analyze the xml for motor configurations. Initialize the motor configurations.
		TestRobotModel model = new TestRobotModel(PathConstants.CONFIG_PATH);
		model.populate();    //
		Solver solver = new Solver();
		solver.configure(model.getMotors(),PathConstants.URDF_PATH);
		
		//solver.setJointPosition(Joint.ABS_Y,90.);
		double[] xyz = solver.getPosition(Joint.ABS_Y);   // Just to top of pelvis
        System.out.println(String.format("%s (0.2,0,.114): xyz = %.2f,%.2f,%.2f ",Joint.ABS_Y.name(),xyz[0],xyz[1],xyz[2]));
    }

}

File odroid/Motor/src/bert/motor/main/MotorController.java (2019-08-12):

/**
 * Copyright 2019. Charles Coughlin. All Rights Reserved.
 *                 MIT License.
 *
 */
package bert.motor.main;

import java.util.ArrayList;
import java.util.HashMap;
import java.util.LinkedList;
import java.util.List;
import java.util.Map;
import java.util.concurrent.locks.Condition;
import java.util.concurrent.locks.Lock;
import java.util.concurrent.locks.ReentrantLock;
import java.util.logging.Logger;

import bert.motor.dynamixel.DxlMessage;
import bert.share.common.BottleConstants;
import bert.share.message.MessageBottle;
import bert.share.message.RequestType;
import bert.share.model.Joint;
import bert.share.model.JointProperty;
import bert.share.model.Limb;
import bert.share.model.MotorConfiguration;
import jssc.SerialPort;
import jssc.SerialPortEvent;
import jssc.SerialPortEventListener;
import jssc.SerialPortException;

/**
 *  Handle requests directed to a specific group of motors. All motors in the 
 *  group are connected to the same serial port. We respond to the group controller
 *  using call-backs. The responses from the serial port do not necessarily keep
 *  to request boundaries. All we are sure of is that the requests are processed
 *  in order. 
 *  
 *  The configuration array has only those joints that are part of the group.
 *  It is important that the MotorConfiguration objects are the same objects
 *  (not clones) as those held by the MotorManager (MotorGroupController).
 */
public class MotorController implements  Runnable, SerialPortEventListener {
	protected static final String CLSS = "MotorController";
	private static Logger LOGGER = Logger.getLogger(CLSS);
	private static final int BAUD_RATE = 1000000;
	private static final int MIN_WRITE_INTERVAL = 100; // msecs between writes (50 was too short)
	private static final int STATUS_RESPONSE_LENGTH = 8; // byte count
	private final Condition running;
	private final DxlMessage dxl;
	private final String group;                 // Group name
	private final Lock lock;
	private final SerialPort port;
	private boolean stopped = false;
	private final MotorManager motorManager;
	private final Map<Integer,MotorConfiguration> configurationsById;
	private final Map<String,MotorConfiguration> configurationsByName;
	private byte[] remainder = null;
	private final LinkedList<MessageBottle> requestQueue;   // requests waiting to be processed
	private final LinkedList<MessageWrapper> responseQueue; // responses waiting for serial results
	private long timeOfLastWrite;

	public MotorController(String name,SerialPort p,MotorManager mm) {
		this.dxl = new DxlMessage();
		this.group = name;
		this.port = p;
		this.motorManager = mm;
		this.configurationsById = new HashMap<>();
		this.configurationsByName = new HashMap<>();
		this.requestQueue = new LinkedList<>();
		this.responseQueue = new LinkedList<>();
		this.lock = new ReentrantLock();
		this.running = lock.newCondition();
		this.timeOfLastWrite = System.nanoTime()/1000000; 
	}

	public String getGroupName() { return this.group; }
	public Map<String,MotorConfiguration> getConfigurations() { return this.configurationsByName; }
	public MotorConfiguration getMotorConfiguration(String name) { return configurationsByName.get(name); }
	public void putMotorConfiguration(String name,MotorConfiguration mc) {
		configurationsById.put(mc.getId(), mc);
		configurationsByName.put(name, mc);
	}

	/**
	 * Open and configure the port.
	 * Dynamixel documentation: No parity, 1 stop bit, 8 bits of data, no flow control
	 * 
	 * At one point, we thought we should initialize the motors somehow.  This is now
	 * taken care of by the dispatcher. The dispatcher:
	 * 	1) requests a list of current positions (thus updating the MotorConfigurations)
	 * 	2) sets travel speeds to "normal"
	 * 	3) moves any limbs that are "out-of-bounds" back into range.
	 */
	public void initialize() {
		LOGGER.info(String.format("%s.initialize: Initializing port %s)",CLSS,port.getPortName()));
		if( !port.isOpened()) {
			try {
				boolean success = port.openPort();
				if( success && port.isOpened()) {
					port.setParams(BAUD_RATE, SerialPort.DATABITS_8, SerialPort.STOPBITS_1, SerialPort.PARITY_NONE);  
					port.setEventsMask(SerialPort.MASK_RXCHAR);
					port.purgePort(SerialPort.PURGE_RXCLEAR);
					port.purgePort(SerialPort.PURGE_TXCLEAR);
					port.addEventListener(this);
				}
				else {
					LOGGER.severe(String.format("%s.initialize: Failed to open port %s for %s",CLSS,port.getPortName(),group));
				}
			}
			catch(SerialPortException spe) {
				LOGGER.severe(String.format("%s.initialize: Error opening port %s for %s (%s)",CLSS,port.getPortName(),group,spe.getLocalizedMessage()));
			}
			LOGGER.info(String.format("%s.initialize: Initialized port %s)",CLSS,port.getPortName()));
		}
	}
	public void stop() {
		try {
			port.closePort();
		}
		catch(SerialPortException spe) {
			LOGGER.severe(String.format("%s.close: Error closing port for %s (%s)",CLSS,group,spe.getLocalizedMessage()));
		}
		stopped = true;
	}
	public void setStopped(boolean flag) { this.stopped = flag; }
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

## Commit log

2018-08-09 Added bill of materials with suppliers/costs
    [BillOfMaterials.ods]
2018-08-10 Added to BOM.
    [BillOfMaterials.ods]
2018-09-10 Skeleton .stl files.
    [MX28_double_rotation_link.STL, MX64_double_rotation_link.STL, camera_support.STL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]
2018-09-19 Keep track of skeletal parts.
    [SkeletonStatus.ods]
2018-10-01 Updated 3d print status.
    [SkeletonStatus.ods]
2018-10-15 First load of reference code.
    [ax12.cfg, config.txt, pylint.cfg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]
2018-10-18 Updated status
    [BillOfMaterials.ods, SkeletonStatus.ods]
2018-10-19 Added delivery times to BOM
    [BillOfMaterials.ods]
2018-11-03 Working gradle build of java
    [SkeletonStatus.ods, ax12.cfg, config.txt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]
2018-11-22 Doc update
    [SkeletonStatus.ods]
2018-11-25 Added Dynamixel port assignments.
    [BillOfMaterials.ods, DynamixelConfiguration.ods]
2018-12-13 Toolchain doc re: jars->java 9 modules
    [DynamixelConfiguration.ods]
2018-12-28 Terminal app runs.
    [SkeletonStatus.ods]
2019-01-05 Massive refactor - snapshot
    [Pose.csv]
2019-01-07 Creaste tables update.
    [Action_empty.csv]
2019-01-09 Progress with named pipes.
    [BillOfMaterials.ods]
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2019-01-14 Prior to replacement of Motor process with threads.
    [Motor.java, MotorGroupHandler.java, Motors.java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]
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2019-01-21 Ready for detailed serial commands.
    [BillOfMaterials.ods]
2019-01-26 Fixes as we debug.
    [RobotMotorModel.java]
2019-01-30 Fixed issue with serializing bottle.
    [MotorController.java]
2019-02-01 Eliminated polling.
    [BillOfMaterials.ods]
2019-02-05 Documentation and build-script updates.
    [BillOfMaterials.ods]
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2019-02-15 Attempt to fix powersupply image rotation.
2019-02-18 Umbilcal images.
    [BillOfMaterials.ods]
2019-02-18 Fix link to step-down circuit.
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2019-03-12 Revert to Java 10 for compatability with Odroid.
    [RobotMotorModel.java]
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2019-04-15 Correctly querying torque (load).
    [JointProperty.java, MotorController.java, MotorGroupController.java]
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2019-04-25 Revamp bluetooth to use bluecove. Pared down to, hopefully, only what we need.
    [DynamixelConfiguration.ods, PoseMap.csv]
2019-04-29 Correct position of ankle to "user" units. First successful write of position.
    [DynamixelConfiguration.ods]
2019-04-29 Right ankle is calibrated.
    [DynamixelConfiguration.ods]
2019-04-30 Can command ankles, knees and elbows. Bluecove moved around for culling.
    [DynamixelConfiguration.ods]
2019-05-01 Head y and z control.
    [DynamixelConfiguration.ods]
2019-05-04 Beginning of code for Pose in Database.
    [DynamixelConfiguration.ods, Pose.csv, PoseMap.csv]
2019-05-22 rfcommserver working still. Devices need to be connected manually ...
    [DynamixelConfiguration.ods]
2019-05-23 Progress with Pose
    [DynamixelConfiguration.ods, Pose.csv, PoseMap.csv]
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2019-05-30 Calibratd all joints except shoulders.
    [DynamixelConfiguration.ods]
2019-05-31 Completed calibration of last joints.
    [DynamixelConfiguration.ods]
2019-06-03 First successful use of SYNCH WRITE
    [Pose.csv, PoseMap.csv]
2019-06-04 Numerous syntax improvemenets.
    [Pose.csv, PoseMap.csv]
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2019-06-08 Added Control project, fixed ANTLR parsing for "go limp"
    [DynamixelConfiguration.ods, Pose.csv]
2019-06-10 Now parse URDF file.
    [Pose.csv]
2019-06-13 Work on Android speech, URDF file interpretation.
    [BillOfMaterials.ods]
2019-06-19 Toward forward kinematics.
    [BillOfMaterials.ods]
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2019-07-15 Fixed issue counting return messages from LIST_PROPERTIES.
    [MotorController.java]
2019-07-15 Corrected response message counting in motor controller
    [MotorController.java]
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2019-07-17 nrser improvements. "attention" is not "straighten up"
    [PoseMap.csv, WhatIsConfiguration.txt]
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2019-07-25 Forward kinematics: correct answer for first joint.
    [Solver.java]
2019-07-26 Significant parsing improvements. Use percent for speed, torque.
    [Pose.csv, PoseMap.csv]
2019-08-02 Added TORQUE_ENABLE as a joint property
    [Pose.csv, PoseMap.csv]
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2019-08-15 Parsing updates.
    [Pose.csv]
2019-08-27 Logic fix for routing through internal controller.
    [Limb.java, MotorController.java, MotorGroupController.java]
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2019-08-30 Ready for video 2 - making a pose.
    [Action_empty.csv, DynamixelConfiguration.ods, Pose.csv]
2019-10-05 Added Blender files for face.
    [blocked_face.scad, blocked_face.stl, blocks.stl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]
2022-06-07 Progress in face cad
    [face-only.blend]
2022-08-31 Cleared to restart development
    [ax12.cfg, config.txt, pylint.cfg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]
2022-09-03 Initial version2 project structure.
    [Action_empty.csv, Pose.csv, PoseMap.csv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]
2022-09-09 Fledgling builds - android and kotlin console.
    [Action_empty.csv, Pose.csv, PoseMap.csv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]
2022-09-29 New kotlin files.
    [Action_empty.csv, Pose.csv, PoseMap.csv]
2022-10-15 BeartSpeak: one compile error.
    [MotorConfiguration.kt]
2022-11-17 Progress - 390 errors remain
    [InternalController.kt]
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2023-02-02 Bert with 184 compile errors remaining.
    [InternalController.kt]
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2023-02-23 65 errors to go.
    [MotorConfiguration.kt]
2023-04-13 Added powerbox drawing.
    [bottom.scad, top.scad]
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2023-06-29 Still trying to write to database in Android.
    [cartoon_head.blend, cartoon_head.obj]
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2023-08-07 Update CAD for powerbox
    [bottom.scad, bottom.stl, top.scad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]
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2023-08-26 Doc updates for Odroid
    [BillOfMaterials.ods]
2023-08-30 Working on shutdown handler
    [BillOfMaterials.ods]
2023-10-20 Start of CAD head back for Odroid N2
    [blocked_face.scad, head_back_N2.scad]
2023-10-20 Further on Odroid N2 head
    [head_back_N2.scad]
2023-10-22 SCAD for head mod for Odroid N2.
    [head_back_N2.scad]
2023-10-23 head_back progress for N2
    [head_back_N2.scad]
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2023-10-26 Head update is close
    [head_back_N2.scad]
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2023-10-29 Final head_back update for Odroid N2.
    [head_back_N2.scad]
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2024-01-09 Fixed speech recognizer thread assignments.
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2024-01-20 Fixed details re: 12V processor power
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2024-02-17 FIxed control in motor controllers.
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2024-02-29 Fixed some issues with configuration.
    [InternalController.kt]
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2024-07-18 SocketManager is PENDING if connection fails to robot
2024-07-20 Major fixes to Speech/Hearing
    [BillOfMaterials.ods]
2024-07-29 Added eye cad files.
    [Bottom Left Lid.stl, Bottom Lid Link (x2).stl, Bottom Right Lid.stl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]
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2024-09-14 Start dealing with JSON requests to Robot
    [PoseMap.csv]
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2024-10-16 Passed range of motion test
    [Pose.csv]
2024-10-25 Updated SQL for pose in "skinny" table
    [Pose.csv, PoseMap.csv, PoseName.csv]
2024-10-28 Partial implementation of JSON message type.
    [PoseName.csv]
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2024-11-07 Revamped database tables for Poses and Actions
    [Action.csv, Action_empty.csv, Pose.csv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]
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2024-11-23 Fixed issue of setting joint rigid
    [InternalController.kt]
2024-11-26 Redesign for distributed pose execution coded.
    [InternalController.kt, MotorConfiguration.kt]
2024-12-01 Independent control of limbs in pose works. Still too much synchronization.
    [InternalController.kt]
2024-12-10 Progress toward internalcontroller fix.
    [InternalController.kt, MotorConfiguration.kt]
2024-12-17 SET_MOTOR_PROPERTY working again. Problem with READ_MOTOR_PROPERTY
    [InternalController.kt]
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2025-01-02 Fix for pose not work after relax
    [InternalController.kt]
2025-01-11 Fixes related to display of dynamic parameters besides angle.
    [PoseJoint.csv]
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2025-02-08 Bug fixes. Torque still not working.
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2025-02-26 Correct analysis of URDF model.
    [PoseJoint.csv]
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2025-05-22 Cleanup of syntax regarding lists
    [PoseJoint.csv]
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2025-06-12 Android fixes and URDF changes.
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2025-09-17 Start of redesign of joint timing protections.
    [MotorConfiguration.kt]
2025-09-25 Actions seem to work
    [PoseJoint.csv]
2025-10-01 Constants for change tolerance.
    [InternalController.kt]
2025-11-15 QL fixes, better bounds checking when creating poses.
    [Action.csv]
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2025-12-18 Corrections to design of JointLinks. Needs testing.
    [MotorConfiguration.kt]
2025-12-25 URDF testing fixes
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2026-01-22 Checkpoint - link redesign
    [InternalController.kt]
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2026-04-01 Front view correct, except ears switched.
2026-04-13 Progress on listing motor attributes. Positions not working
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2026-05-13 Fixed angle of IMU at 180.
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2026-05-19 Debugging for issue with setting current status.
    [BillOfMaterials.ods]
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
